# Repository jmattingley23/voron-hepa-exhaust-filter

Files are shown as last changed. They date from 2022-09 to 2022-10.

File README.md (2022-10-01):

# Voron HEPA Exhaust Filter
An upgraded exhaust filter for Voron printers that features toolless, quick swappable HEPA particulate filters 

## Demo

https://user-images.githubusercontent.com/7289536/190971695-ee978da5-1548-4ee2-b269-1e507fdcde98.mp4

## Background

Improves the stock exhaust filter by ditching the crappy solder fume filter and replaces it with proper HEPA particulate filters in a redesigned housing.  These filters get a tight seal against the enclosure and can easily be swapped out using the toolless release mechanism without the need to fumble around the back of the printer with hex keys.  The filters also load in from the side instead of the back so you don't have to move your printer away from the wall to change them.  I wanted it to be easy as possible to change filters because I knew if it wasn't I wouldn't actually rotate them on a regular schedule.

This mod is designed to work alongside the [Nevemore](https://github.com/nevermore3d/Nevermore_Micro) activated carbon air scrubber, and adds particulate filtration (nevermore carbon only removes VOCs) as well as a slight negative pressure inside the chamber to help prevent diffusion.

## BOM



I made an effort to have the BOM be as streamlined as possible, and as such almost all of the hardware from the original exhaust filter can be re-used.  If you're upgrading from an existing V2 or Trident BOM, you'll only need to purchase:

- 4x M3x30 SHCS
- 2x M3 heat set inserts
- 1x+ 11cm x 5.5cm Roomba HEPA Filter
    - More info on filter sourcing [here](#hepa-filter-selection)
- 6cm of 5mmx1mm foam tape

If you are not coming from an existing build you will need the full BOM, which is **everything above** *plus*:

- 4x M3x30 SHCS (8 total)
- 2x M3x12 SHCS
- 8x M3 heat set inserts (10 total)
- 2x M5x10 BHCS
- 2x M5 t-nut
- 1/8" BSPP Bowden coupler
- 1x 60x60x20 Axial Fan

#### HEPA Filter Selection

This mod was designed around using 11cm x 5.5cm replacement Roomba HEPA filters.  This was done for a number of reasons including:

- They are reasonably high quality
- They are readily available for cheap with fast shipping from a variety of sellers on sites like Amazon (no more 2 month lead time for Aliexpress filters)
- They come built into a rigid plastic housing which allows us to clamp against them for a tight seal
- They have a protuding tab on the bottom edge for the toolless release mechanism to hook onto

These are the exact ones I purchased: https://smile.amazon.com/gp/product/B00K7DMEJ0, though similar items are available from a variety of vendors and should all be fine.

## Assembly

Assembly is pretty straightforward, everything is built up in a big stack.  I'll outline the main points here but the CAD model is your friend if you get stuck.
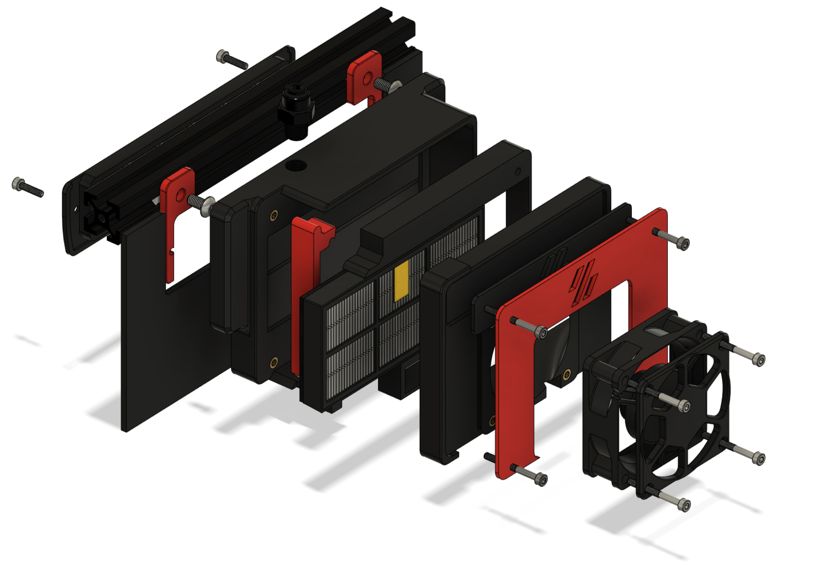
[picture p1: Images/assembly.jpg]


---
1. Add a strip of tape along the length of the inside face of the door piece.  This helps get an airtight seal against the filter frame and provides a bit of tension for the latching mechanism.


2. Start the main assembly by securing the filter mounts to the frame with the M5x10 BHCS and t-nuts


3. Drive 2x M3x12 SHCS through the exhaust grill into the backplate to attach both pieces (same method as on the stock exhaust).  Now is also a good time to route your bowden tube and fish your fan connector through.


4. Pass the fan cable through the filter surround piece and route it as shown.  The empty space is for stuffing any excess cable in.

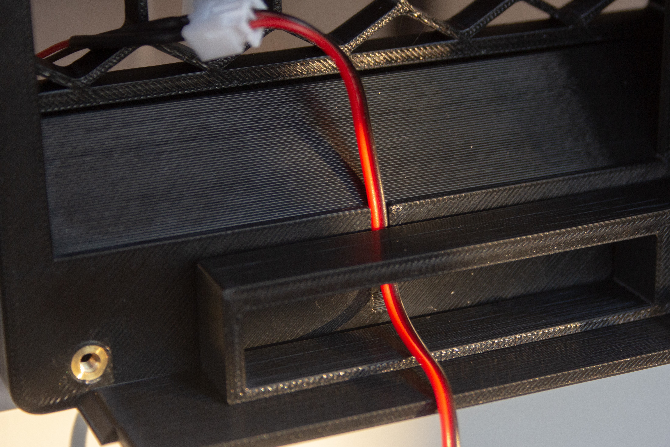
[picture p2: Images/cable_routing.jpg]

5. Use 4x M3x30 SHCS to secure the rest of the printed parts to the backplate, being sure to add the door piece to the bottom left screw.  Tighten down the two fasteners on the right side, and snug up the left ones to the point where everything is sealed and secure, but does not interfere with the door opening and closing.  It should open and close with relative ease and a satisfying snap.
    - Also, I'd recommend adding a bit of tape to secure the fan cable so it's not flopping around in the path of the filter sliding in and out.  You can use whatever but I found that the same foam tape actually holds very well.  


6. Use the remaining 4x M3x30 SHCS to secure the fan and decorative fan grill (you want the sticker side of the fan facing outwards such that the fan is drawing air out of the chamber and across the filter).

## See Also

[Nevermore](https://github.com/nevermore3d/Nevermore_Micro) - activated carbon air scrubber that this mod is designed to be paired with  
[VEFACH](https://github.com/VoronDesign/VoronUsers/tree/master/printer_mods/KevinAkaSam/VEFACH) - An alternative to this+nevermore, that features particulate filtration and activated carbon all in one unit

---

jmatt#7569

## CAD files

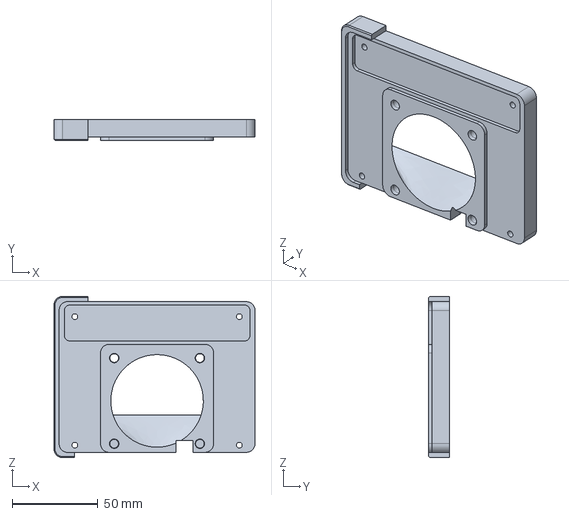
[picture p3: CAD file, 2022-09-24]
CAD/fan_mount.step
117.3 x 12.0 x 94.1 mm

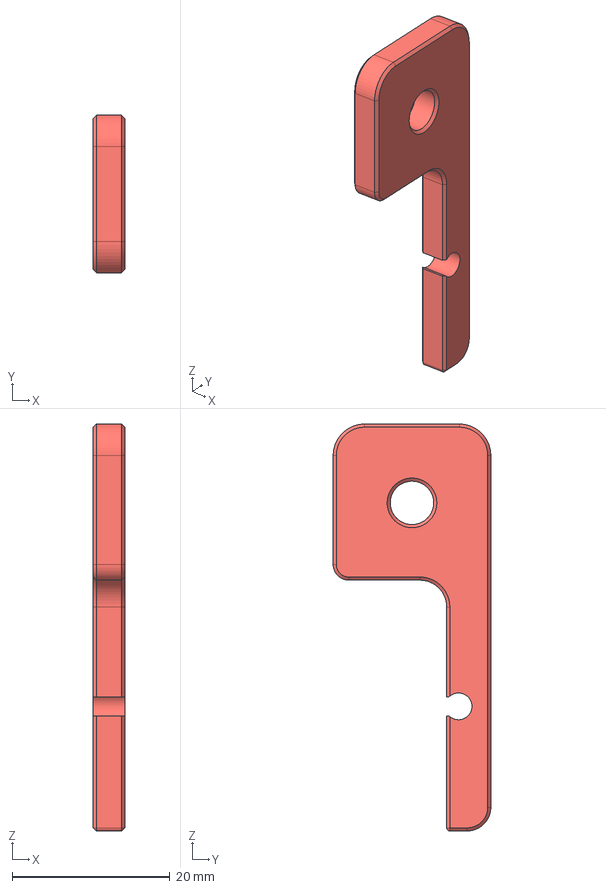
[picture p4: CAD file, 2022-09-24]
CAD/[a]_exhaust_filter_mount_x2.step
4.00 x 20.0 x 51.6 mm

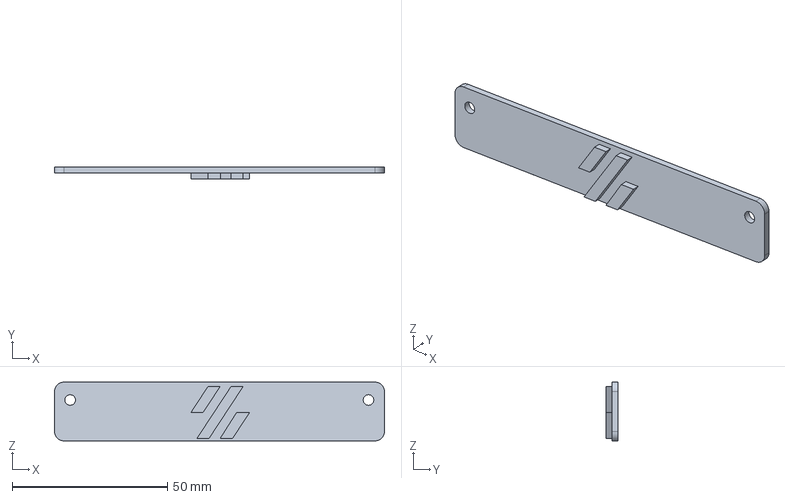
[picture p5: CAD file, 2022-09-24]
CAD/voron_logo.step
106.2 x 3.90 x 18.9 mm

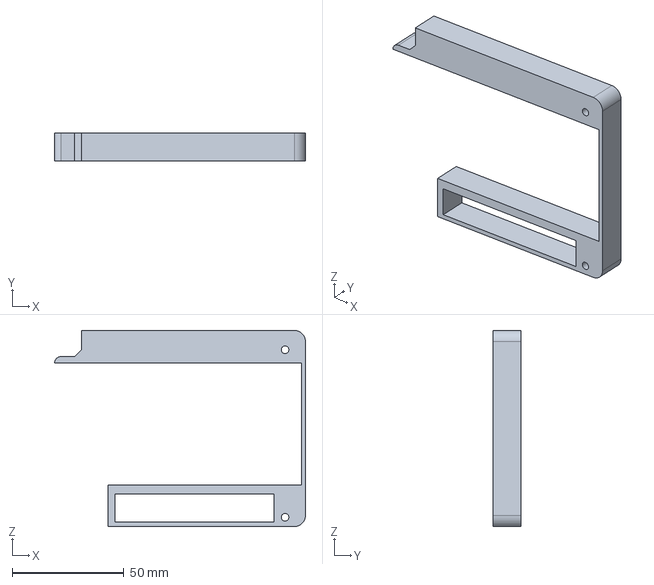
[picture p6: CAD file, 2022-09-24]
CAD/filter_surround.step
112.4 x 12.8 x 87.8 mm

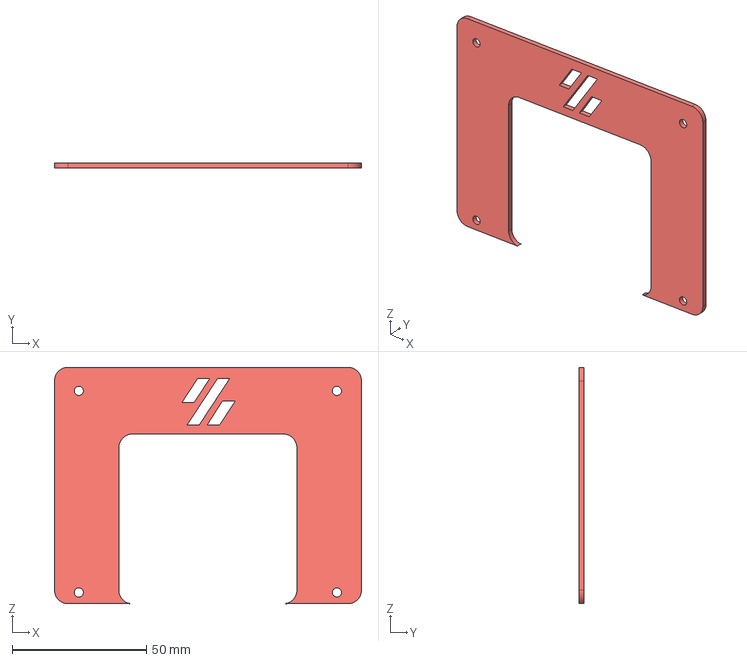
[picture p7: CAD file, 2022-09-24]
CAD/[a]_accent_plate.step
114.2 x 1.90 x 87.9 mm

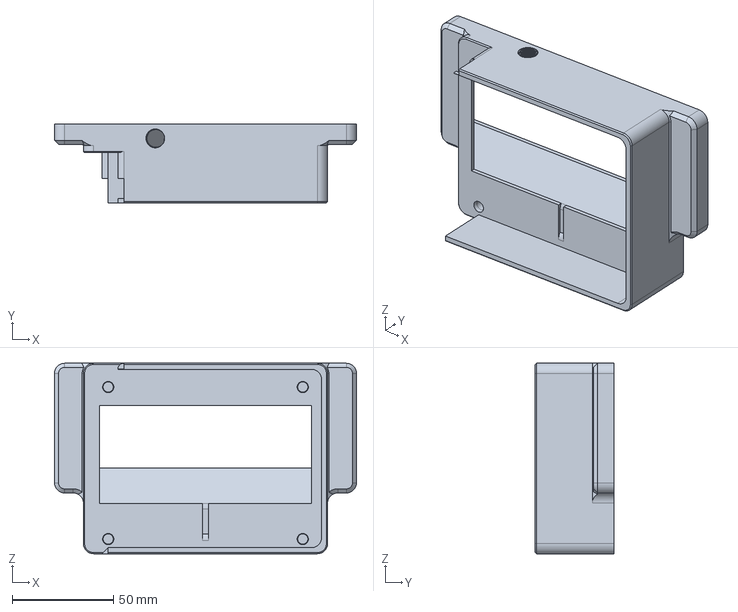
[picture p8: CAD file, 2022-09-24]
CAD/backplate.step
149.0 x 38.8 x 94.0 mm

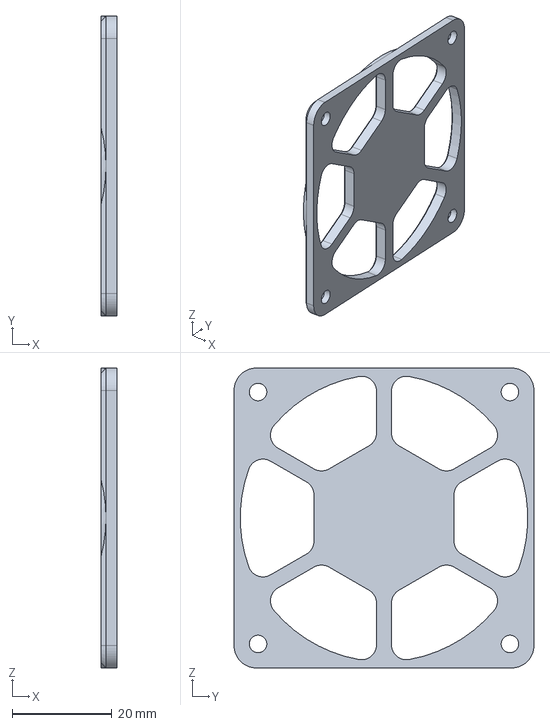
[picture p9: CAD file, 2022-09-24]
CAD/fan_grill.step
3.20 x 60.0 x 60.0 mm

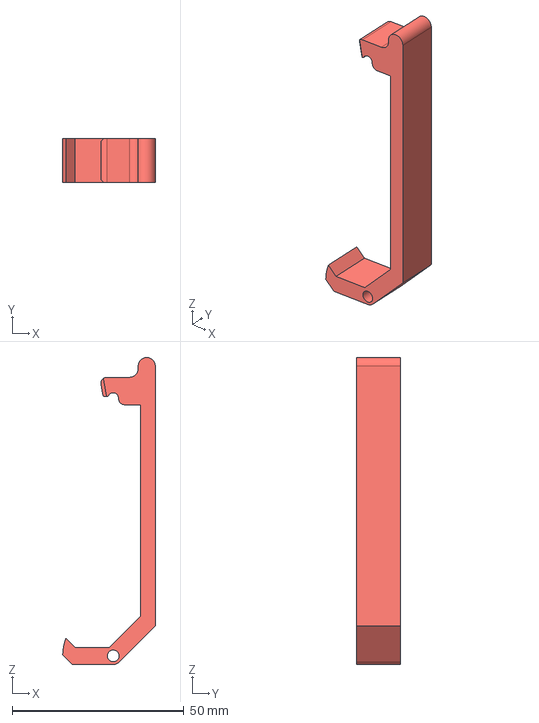
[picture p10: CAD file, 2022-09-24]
CAD/[a]_door.step
27.0 x 12.8 x 89.2 mm

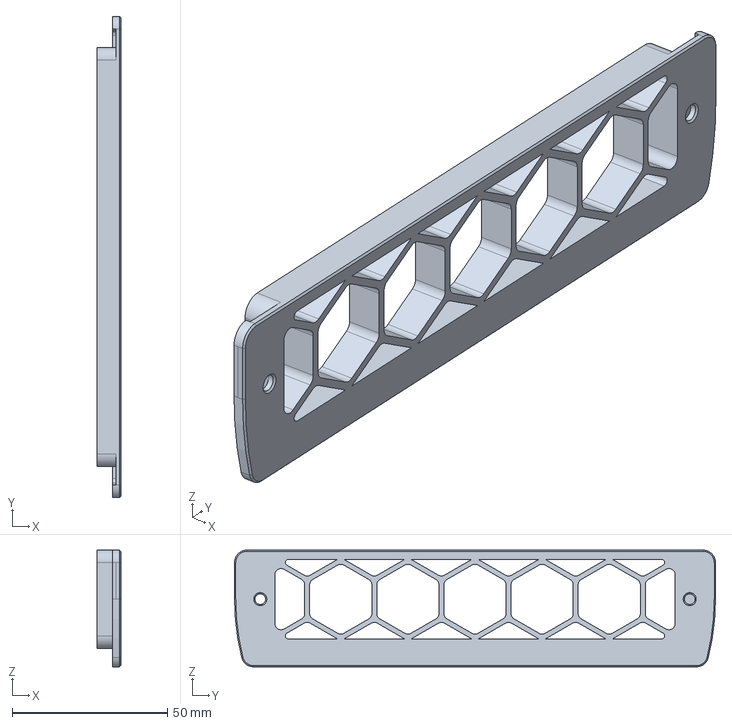
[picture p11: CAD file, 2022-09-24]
CAD/exhaust_filter_grill.step
7.60 x 154.8 x 37.6 mm

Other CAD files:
STLs/[a]_accent_plate.stl
STLs/[a]_door.stl
STLs/[a]_exhaust_filter_mount_x2.stl
STLs/backplate.stl
STLs/exhaust_filter_grill.stl
STLs/fan_grill.stl
STLs/fan_mount.stl
STLs/filter_surround.stl
STLs/voron_logo.stl

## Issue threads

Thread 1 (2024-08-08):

Threaded Insert Size

ElectrodeYT, 2024-08-08:
What size of threaded inserts are we supposed to use for this? The insert sizes are not sized correctly for VORON inserts, and are not sized correctly for every other size of M3 insert I could find.

jmattingley23, 2024-08-10:
Sorry about that, I use these: https://www.mcmaster.com/94180A331/

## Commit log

2022-09-24 Add CAD & STLs
    [[a]_accent_plate.step, [a]_accent_plate.stl, [a]_door.step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]
2022-09-24 Align naming scheme
    [[a]_exhaust_filter_mount_x2.step, [a]_exhaust_filter_mount_x2.stl, exhaust_filter_grill.step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]
